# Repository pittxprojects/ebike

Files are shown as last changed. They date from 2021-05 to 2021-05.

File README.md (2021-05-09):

# DIY EBike Battery System

The main objective of this engineering project was to design a mount that allows a DIY E-bike to receive power from a commercial power tool battery. More specifically, we designed the mount to accept the RYOBI 40-Volt lithium-ion high-capacity battery. The intentions for this scope of design are as follows:

- Employ the economies of scale that are soon to come for lithium-ion batteries
- Take advantage of the safety features already incorporated in the battery
- Provide a battery solution for an E-bike that is easy to source and replace

Included in this repository is:
- A slide deck containing our written documentation on the project
- The Fusion 360 files of our part and the associated components
- The .stl files of our part for 3D printing

Our how-to video can be found [here].
## Authors & Contributors
_This project was conducted as part of the Spring 2021 XProject cohort. The XProjects are administered by the Innovation, Design, and Entrepreneurship Department at the Swanson School of Engineering at the University of Pittsburgh._

- Maya Roman – Junior ME Student
- Peter DeNicola – Junior ME Student
- John Rozzo – Sophomore EE Student
- Nick Bohn – Senior ME Student

- Stephen Spencer – Project Sponsor
- Brandon Barber – Project Coordinator
- Daniel Yates – Project Coordinator
- Dr. William Clark – Project Coordinator

- Thick Bikes (Pittsburgh, PA) – Bike Donor

## License



This work is licensed under a [Creative Commons Attribution-NonCommercial-ShareAlike 4.0 International License].

[//]: # (These are reference links used in the body of this note and get stripped out when the markdown processor does its job. There is no need to format nicely because it shouldn't be seen. Thanks SO - http://stackoverflow.com/questions/4823468/store-comments-in-markdown-syntax)

   [here]: <https://youtu.be/FgjxSFlo72g>
   [Creative Commons Attribution-NonCommercial-ShareAlike 4.0 International License]: <http://creativecommons.org/licenses/by-nc-sa/4.0/>

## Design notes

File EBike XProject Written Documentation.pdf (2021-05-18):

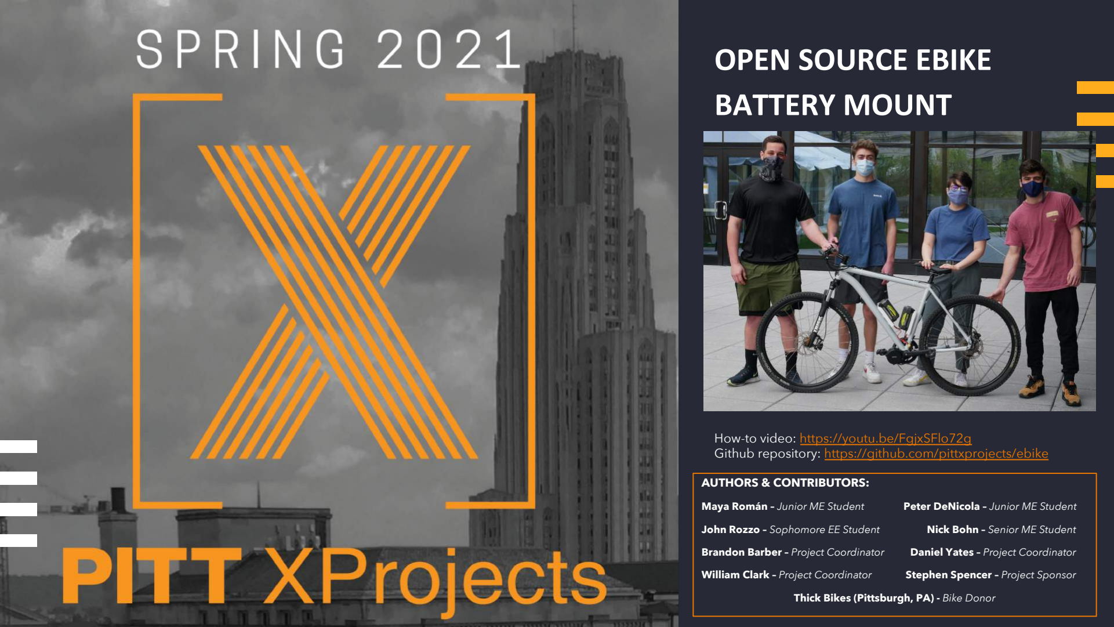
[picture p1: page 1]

### OPEN SOURCE EBIKE BATTERY MOUNT

AUTHORS & CONTRIBUTORS:
Maya Román – Junior ME Student | Peter DeNicola – Junior ME Student
John Rozzo – Sophomore EE Student | Nick Bohn – Senior ME Student
Brandon Barber – Project Coordinator | Daniel Yates – Project Coordinator
William Clark – Project Coordinator | Stephen Spencer – Project Sponsor
Thick Bikes (Pittsburgh, PA) - Bike Donor

How-to video: https://youtu.be/FgjxSFlo72g
Github repository: https://github.com/pittxprojects/ebike

### Project & General Design Overview

The main objective of this engineering project was to design a mount that allows a DIY E-bike to receive power from a commercial power tool battery. More specifically, we designed the mount to accept the RYOBI 40-Volt lithium-ion high-capacity battery. The intentions for this scope of design are as follows:

v Employ the economies of scale that are soon to come for lithium-ion batteries
v Take advantage of the safety features already incorporated in the battery v Provide a battery solution for an E-bike that is easy to source and replace

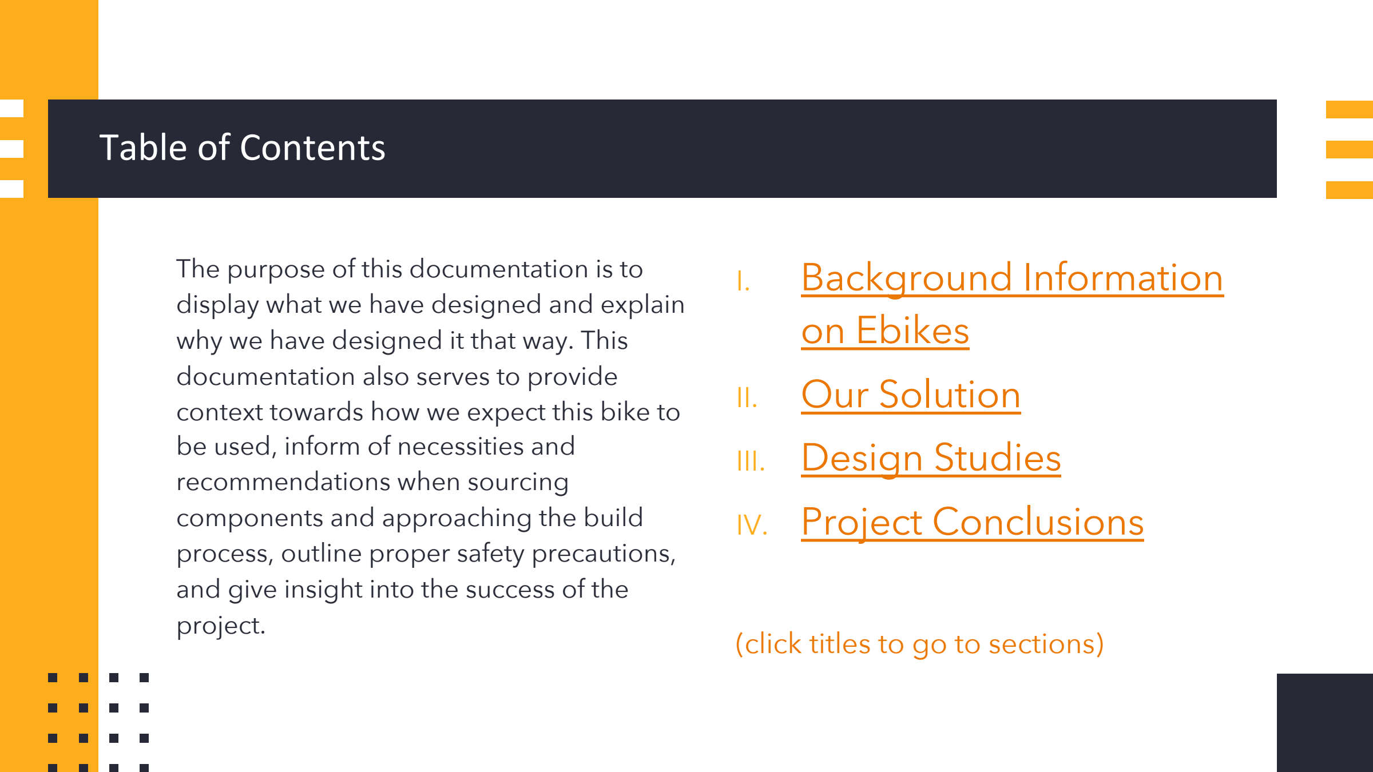
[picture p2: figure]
Table of Contents; The purpose of this documentation is to; why we have designed it that way. This documentation also serves to provide; be used, inform of necessities and recommendations when sourcing components and approaching the build; project.; I. Background Information on Ebikes II. Our Solution III. Design Studies IV. Project Conclusions; (click titles to go to sections)

display what we have designed and explain

context towards how we expect this bike to

process, outline proper safety precautions, and give insight into the success of the

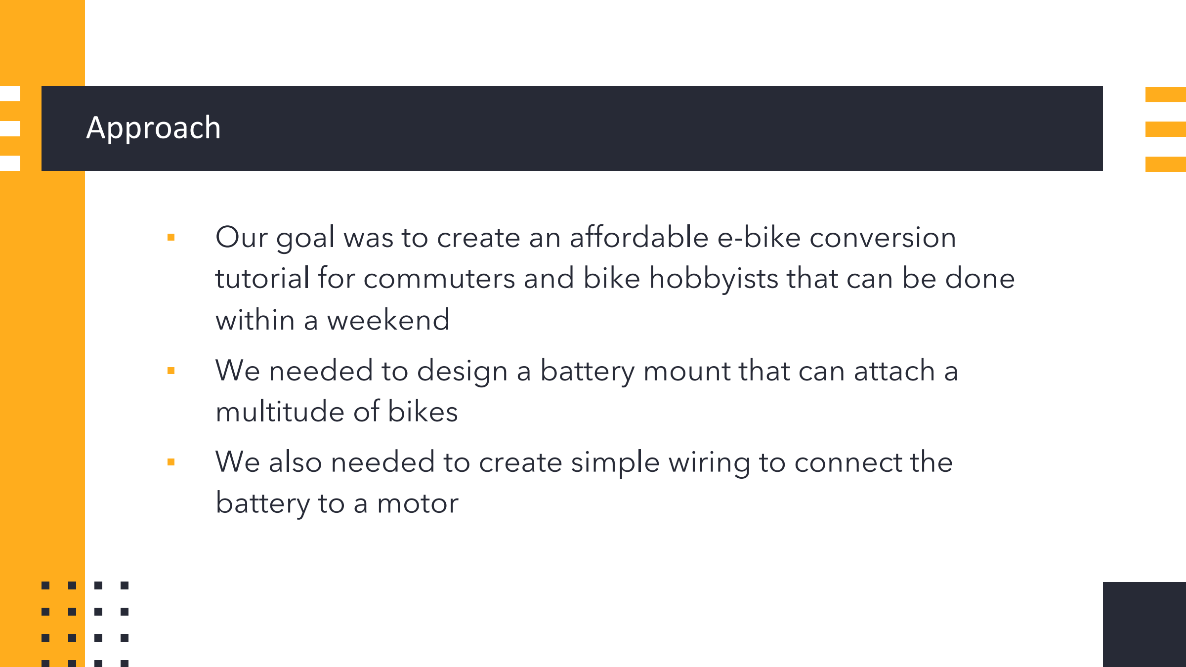
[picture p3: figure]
Approach; within a weekend; multitude of bikes; battery to a motor

### - Our goal was to create an affordable e-bike conversion tutorial for commuters and bike hobbyists that can be done

### - We needed to design a battery mount that can attach a

### - We also needed to create simple wiring to connect the

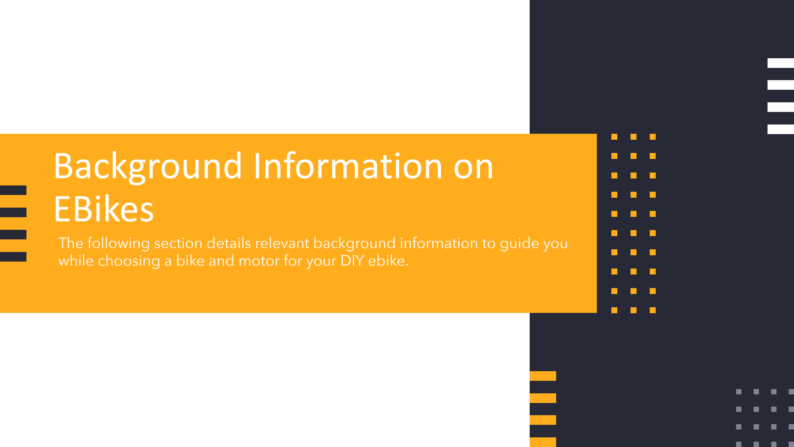
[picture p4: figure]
Background Information on EBikes

The following section details relevant background information to guide you while choosing a bike and motor for your DIY ebike.

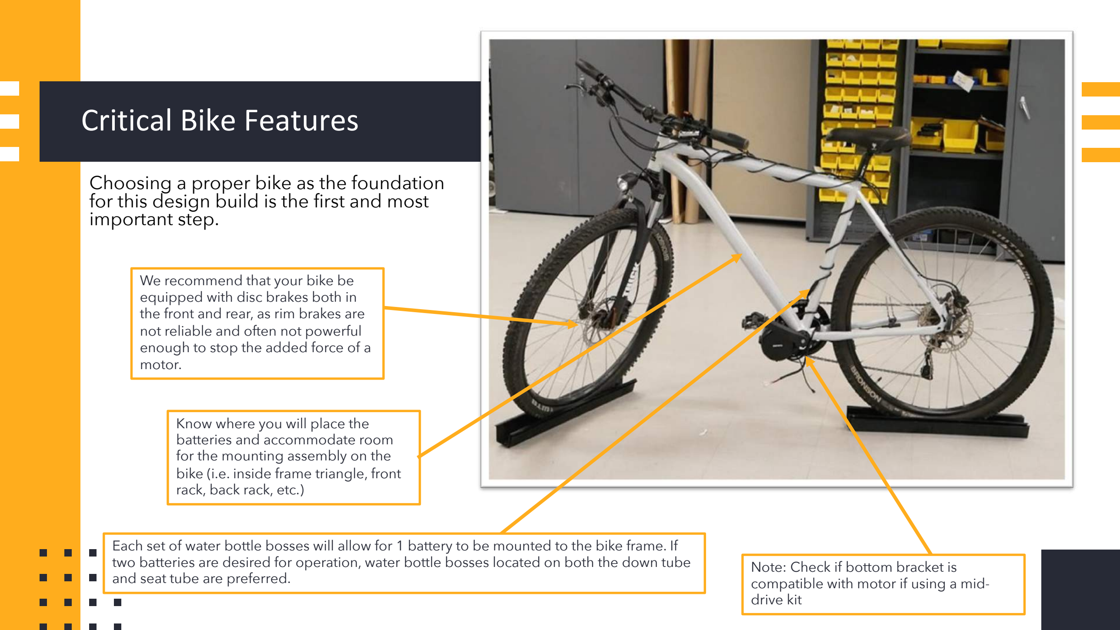
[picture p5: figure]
Critical Bike Features; important step.; We recommend that your bike be equipped with disc brakes both in the front and rear, as rim brakes are not reliable and often not powerful enough to stop the added force of a motor.; Know where you will place the batteries and accommodate room for the mounting assembly on the bike (i.e. inside frame triangle, front rack, back rack, etc.); and seat tube are preferred.; Note: Check if bottom bracket is compatible with motor if using a mid- drive kit

Choosing a proper bike as the foundation for this design build is the first and most

Each set of water bottle bosses will allow for 1 battery to be mounted to the bike frame. If two batteries are desired for operation, water bottle bosses located on both the down tube

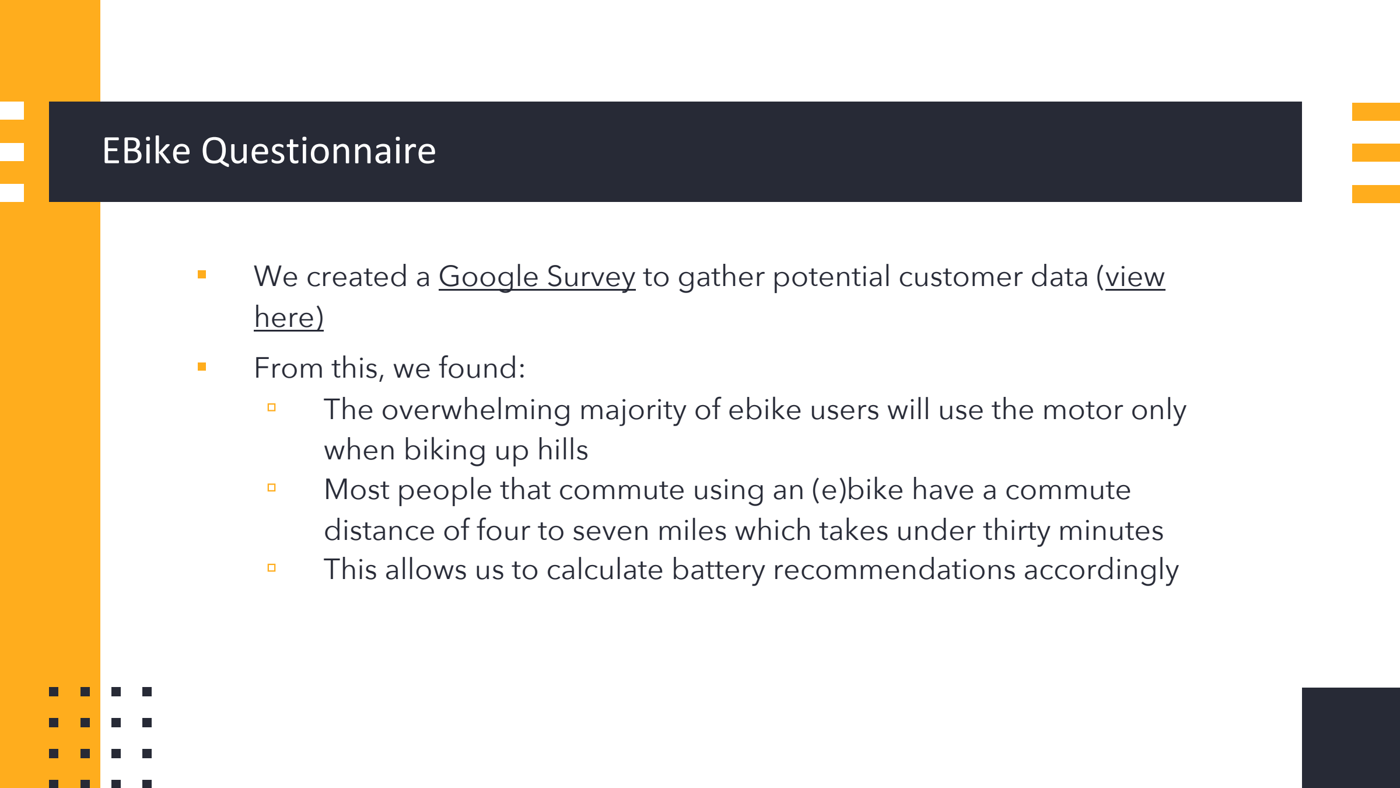
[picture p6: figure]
EBike Questionnaire; here) ▪ From this, we found:; when biking up hills

- We created a Google Survey (https://docs.google.com/forms/d/1E784Fk50arTw0hEiAAEJZYgr2MPm3P4Kt-JPYNBbJBc/edit) to gather potential customer data (view
- The overwhelming majority of ebike users will use the motor only
- Most people that commute using an (e)bike have a commute distance of four to seven miles which takes under thirty minutes
- This allows us to calculate battery recommendations accordingly

### Motor Selection

Motor Power Rating
If the use case of the motor is in a hilly area like Pittsburgh, a motor smaller than 500 W should not be considered. A 250 W motor would usually work for a rider less than 200 lbs if the use case is flat terrain. For very heavy riders, very steep and hilly terrain, or use cases where fast and very powerful performance is desired, 750-1000 W motors should be considered.

### Motor Selection

Peak Power
Additionally, one should consider the peak power (wattage) they will be able to receive with their combined motor and battery setup. This can be calculated by multiplying the Amperage rating of the motor controller (which determines the maximum current that can instantaneously be supplied to the motor) by the voltage of your battery setup. Usually, the peak power will be greater than the wattage that the motor is rated for. For example, a 500 W motor with a 25 Amp controller attached to a 40 V battery setup will experience a peak power of 1000 W. This will be an accurate representation of the power you can expect when you twist the throttle.
!"#$ %&'"( | = | *#+. *&-&( .&/-(&00"( #*% (#-1/2 | ∗ [5#--"(6 7&0-#2"]

### Motor Selection

Motor Type
There are two main types of motor styles used for powering ebikes:
Mid-drive
Mid-drive motors attach at the bike’s bottom bracket, driving the rear wheel in the same way the pedals drive the bike. Mid-drive motors allow you to shift through the bikes gears and provides high power.
Hub drive
Hub drive motors involve replacing one (or sometimes both) of your bike’s wheels with a wheel with a motor at the hub.

### Motor Selection

Mid-Drive Motor | Hub Motor
Higher torque/power since motor directly drives the crank | Decreased torque/performance due to more losses since motor drives rear or front wheel
Maintenance and service is very easy | Service can be complicated for even changing a flat tire
Improved handling by positioning close to the bikes center of gravity creating the feel of riding a traditional bike | Weight is distributed unevenly across the bike either towards the front or rear tire, creating an unnatural ride
Expensive | Cost-effective

### Battery Selection

The problem presented to us by our sponsor related to battery selection for DIY ebikes. People converting bikes to ebikes on their own face the decision to spend a lot of money on proprietary batteries that are large and expensive, or spend less money on less safe batteries. The power tool battery chosen for this project was a RYOBI 40V 4Ah due to the brands popularity and reputation, and battery availability.

### Battery Selection

Battery Overview | Price per Kilowatt hour Comparison (based on large home improvement retailer pricing)
| RYOBI 40V 7.5Ah | $763.33/kWh
| RYOBI 40V 6Ah | $745.82/kWh
| RYOBI 40V 5Ah | $795.00/kWh
| RYOBI 40V 4Ah | $900.00/kWh
| RYOBI 40V 2Ah | $1237.50/kWh

Our sponsor had us
use two RYOBI 40V
4Ah batteries to power
the bike.
(Battery Manual) (https://images.thdstatic.com/catalog/pdfImages/35/357388b5-188b-4d52-b208-4c9af14d54f3.pdf)

### Range Calculations

You can estimate your range based on your battery combination’s total energy capacity and your ebike’s efficiency based on your riding conditions.
Energy Capacity:
The power your battery selection can provide your ebike is based on the batteries’ voltage, their Ah capacity, and how many batteries you use.
!"#$% | = | '"()*+$ | ∗ | -*!*-.)/ | ∗ | # "1 2*))$%.$3
In our case, with two 40V, 4Ah batteries, our battery system would be capable of providing 320 Wh of energy in one charge:
40 6 ∗ 4 7ℎ ∗ (2 2*))$%.$3) = 320 =ℎ

Efficiency:
On average, going 20mph on flat terrain, an ebike has an efficiency of about 25Wh/mi using just the throttle, with no pedal contribution. The efficiency while using pedal assist, but still assuming a speed of 20mph on flat terrain is closer to 15Wh/mi.
Many factors affect the actual efficiency, including total load (weight of rider, bike, and cargo), wind speed and direction, road conditions (paved, gravel, dirt, etc), aerodynamics of your bike, hill grades, etc.
Check out this page (https://www.ebikeaholic.org/ebike-range-calculator) for a more in depth efficiency estimation.

### Range Calculations

Total Range:
To find your battery combination’s total range on one charge, simply divide the energy capacity by the efficiency.

!"#$%&#!' (&)*! =

[!)!(*- .&/&.$#-]
[!"#$%&#!' !11$.$!).-]

This means that in our case, with two 4Ah 40V batteries, we would have a range of about 12.8 miles using just the throttle, and about 21.3 miles if we use pedal assist – assuming we’re going 20mph on flat terrain.
320 5ℎ
25 5ℎ/%$

= 12.8 %$<!" #ℎ(=##<! =)<-

320 5ℎ
15 5ℎ/%$

= 21.3 %$<!" >$#ℎ /!'&< &""$"#

Use these calculations as guidelines rather than hard rules to help you decide which battery or battery combination to use. Remember to give yourself a margin between the range you need and the range your battery system can provide.

# Our Solution

The following section details the specifics of how to make our DIY Battery System. This section supplements our how-to video. (https://youtu.be/FgjxSFlo72g)

### Our Battery System

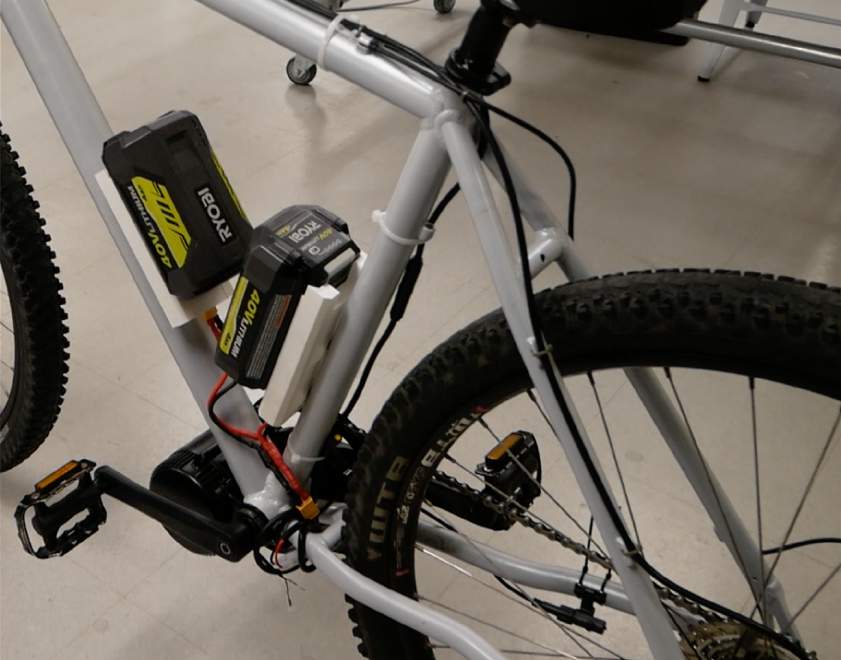
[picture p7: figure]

Our system consists of two RYOBI 40V 4Ah lithium ion batteries attached to the ebike via mounts we designed that connects in parallel to the motor via a Y-harness.

### Our Battery System

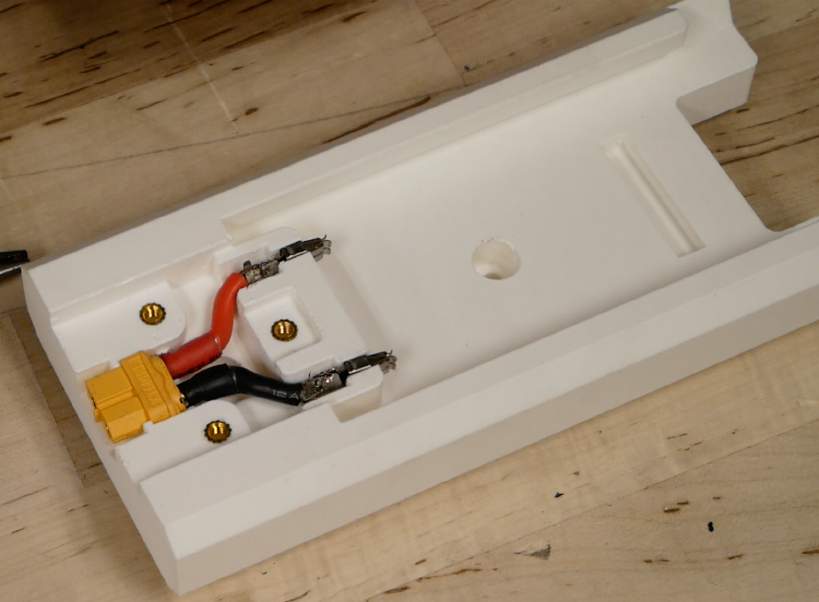
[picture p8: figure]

The mount features rails for the battery to slide into, a slot for the battery’s latch to lock into, two mounting holes to attach the mount to the bike, geometry to hold the internal harness in place and mounting points for a wire cover.

### Critical Dimensions

The critical dimensions of the battery mount are ones we caution against changing if you adjust the CAD model or design your own based on ours. These dimensions are detailed in the next slide, and the critical dimension drawing on our Github repository. The key dimensions are the battery mating profile, the size and position of notches for power timer tabs, the position of power timer timer slots in relation to each other and the locking tab, and the height between the top face that touches the battery and the mounting point on bike (for hand access to battery release tab)

### Critical Dimensions

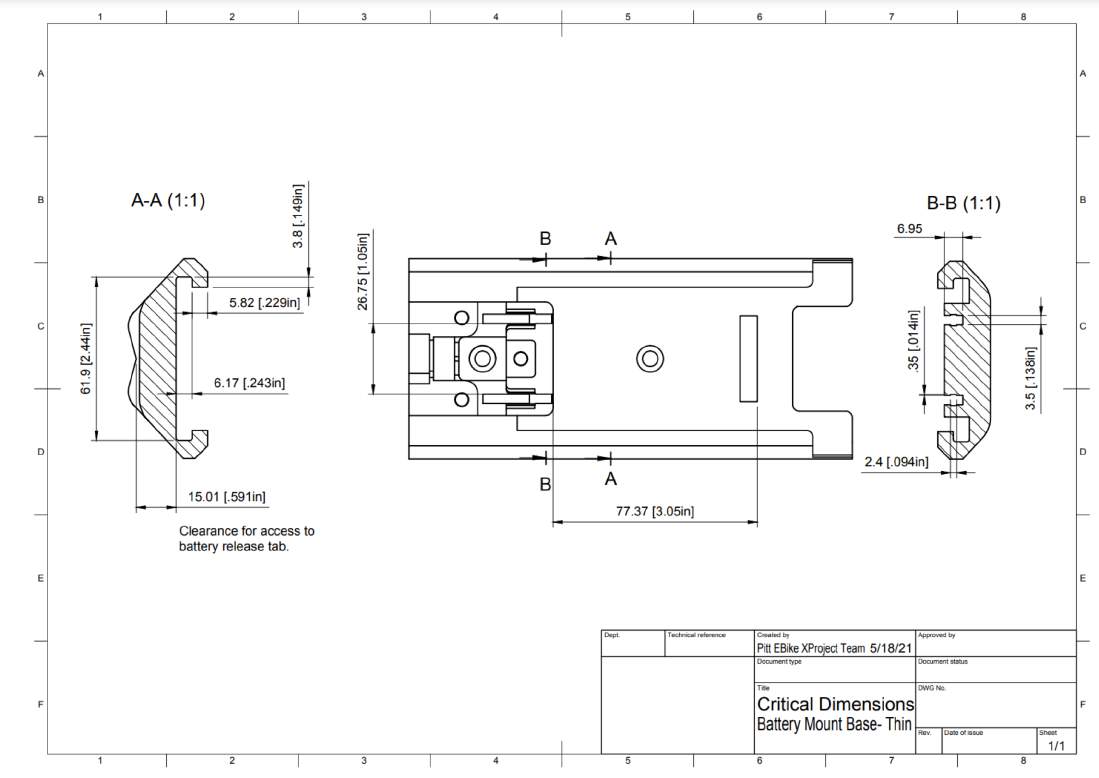
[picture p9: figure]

Bill of Materials

Item | Qty | Vendor | Link | Unit Price | Total Price
M5x0.8 12mm bolts | 4 | McMaster-Carr | https://www.mcmaster.com/92095A210/ | $8.66/50 | $8.66
6-32 ½" bolts | 6 | McMaster-Carr | https://www.mcmaster.com/91251A148/ | $9.59/100 | $9.59
Heat set threaded inserts for 6-32 bolts | 6 | McMaster-Carr | https://www.mcmaster.com/94459A280/ | $10.12/50 | $10.12
24-12 AWG stranded wire (more on wire sizing later) | ~1ft black, ~1ft red | Amazon | https://www.amazon.com/BNTECHGO-Silicone-Flexible-Strands-Stranded/dp/B01ABOPMEI (https://www.amazon.com/BNTECHGO-Silicone-Flexible-Strands-Stranded/dp/B01ABOPMEI) | $12.98/20ft | $12.98
XT60 connector pair, male and female | 3 pairs | Amazon | https://www.amazon.com/Upgrade-Female-Bullet-Connectors-Battery/dp/B07VRZR5TL (https://www.amazon.com/Upgrade-Female-Bullet-Connectors-Battery/dp/B07VRZR5TL) | $8.99/12 pairs | $8.99
Standard power timer contacts | 4 | Digi-Key | (10-11 AWG) (https://www.digikey.com/en/products/detail/te-connectivity-amp-connectors/963709-1/2332255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) (11-13 AWG) (https://www.digikey.com/en/products/detail/te-connectivity-amp-connectors/927824-2/2332032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) (13-17AWG) (https://www.digikey.com/en/products/detail/te-connectivity-amp-connectors/927833-1/2332041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) | $00.74 $00.40 $00.30 | $2.96
3D printer filament (Village Plastics PLA) | ~59m | - | - | - | -
Heat shrink (we used 3/8" and ¼" 3:1) | ~16 pieces | Amazon | https://www.amazon.com/Wirefy-275-Heat-Shrink-Tubing/dp/B084GWYX42 (https://www.amazon.com/Wirefy-275-Heat-Shrink-Tubing/dp/B084GWYX42) | $13.95/275 pcs | $13.95
Solder | - | - | - | - | -
RYOBI 40V 4Ah batteries | 2 | Home Depot | https://www.homedepot.com/p/RYOBI-40-Volt-Lithium-Ion-4-Ah-High-Capacity-Battery-OP4040A1/307973316 (https://www.homedepot.com/p/RYOBI-40-Volt-Lithium-Ion-4-Ah-High-Capacity-Battery-OP4040A1/307973316) | $144 | $288
BAFANG 500W mid-drive motor kit | 1 | Amazon | https://www.amazon.com/gp/product/B07PQM7167/ref=ppx_yo_dt_b_asin_title_o04_s00?ie=UTF8&psc=1 (https://www.amazon.com/gp/product/B07PQM7167/ref=ppx_yo_dt_b_asin_title_o04_s00?ie=UTF8&psc=1) | $404 | $404
Donor bike | 1 | - | - | - | -
TOTAL | $759.25

### Bill of Materials

- Note on the BOM: the only item we recommend being exactly the same as what we used are the power timer contacts which interface with the battery terminals. All other materials can be what you have on hand or find at a hobby store or website. We provided the material links more as a helpful reference than as the exact places you must buy parts.

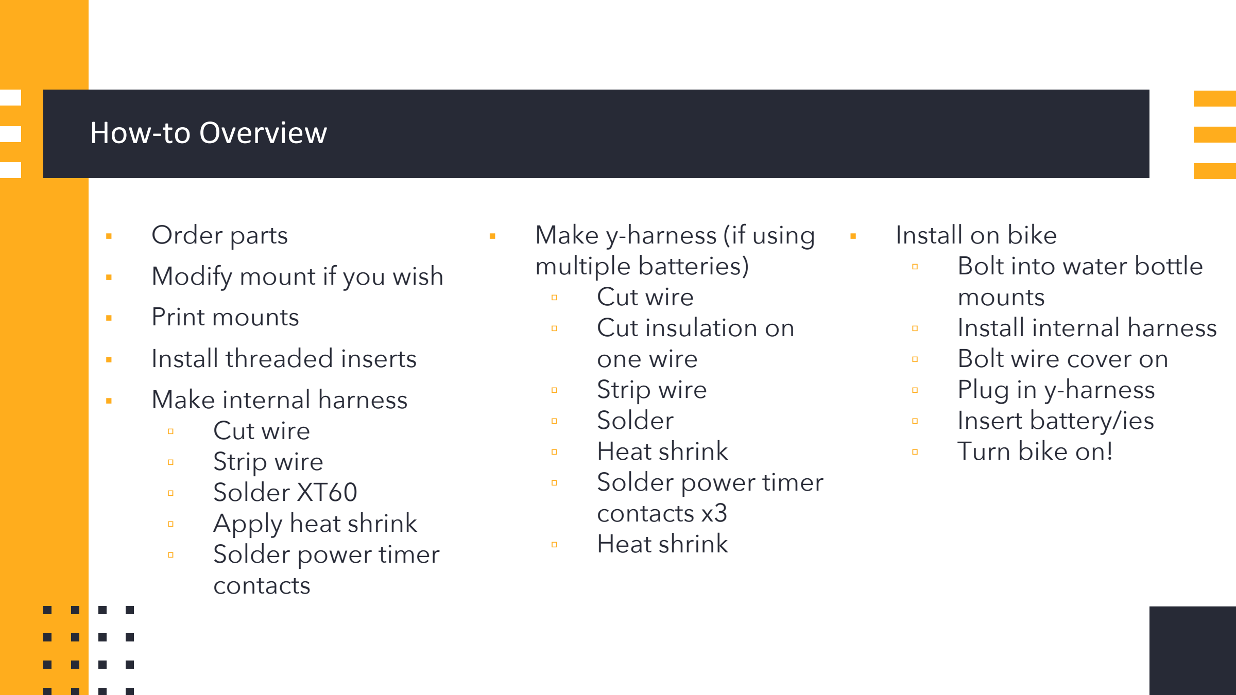
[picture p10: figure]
How-to Overview; ▪ Order parts ▪ Modify mount if you wish ▪ Print mounts ▪ Install threaded inserts ▪ Make internal harness ▫ Cut wire ▫ Strip wire ▫ Solder XT60 ▫ Apply heat shrink ▫ Solder power timer contacts; ▪ Make y-harness (if using multiple batteries) ▫ Cut wire ▫ Cut insulation on one wire ▫ Strip wire ▫ Solder ▫ Heat shrink ▫ Solder power timer contacts x3 ▫ Heat shrink; ▪ Install on bike ▫ Bolt into water bottle mounts ▫ Install internal harness ▫ Bolt wire cover on ▫ Plug in y-harness ▫ Insert battery/ies ▫ Turn bike on!

### Order Parts

- You can use our Bill of Materials as a reference for your project, however you don’t have to use all of the same exact parts as we did.
- It’s probably a good idea to get a few extra of the components like the threaded inserts, the power timer contacts, and the XT60 connectors if possible just in case something goes wrong while putting it all together
- Make sure the get heat shrink and power timer contacts that are compatible with your chosen wire gauge
- The next slide details how to choose your wire gauge

### Electrical Safety

Loose connections, power overloads (excessive current), and short circuiting can all melt your wire and cause electrical safety hazards!
To prevent excessive current draw, you must use wires properly rated for current that you expect to put through them.
Ideally, your battery system should be the current-limiting factor in your ebike system, meaning the total amerage capacity of your battery(ies) should be greater than the max current your motor controller is rated for.
That was not the case for our setup, and our motor controller was rated for a maximum of 25 Amps, so we used 12 AWG wire to incorporate a margin of safety in the worst case scenario of maximum current draw.
Use the chart on the right (from here) (https://www.engineeringtoolbox.com/wire-gauges-d_419.html) to help you determine which wire gauge is appropriate for the current that will go through your system.

Max. Current
Load (amps)

### Modify the Model

- The default model allows you to mount two 40V 4Ah RYOBI batteries on both sets of water bottle mounting points, however you can edit the model to function as you need. You can download the Fusion 360 models from our Github repository. (https://github.com/pittxprojects/ebike)
- To move the mounting hole position in the model, edit Sketch 11
- To remove the v-notch geometry, suppress Extrude 13
- You'll have to edit the counterbore in Hole 1 so that there’s enough thickness for the two mounting bolts to clamp on to
- To adjust the battery mating geometry, edit Sketch 2, renamed “battery mating geometry”

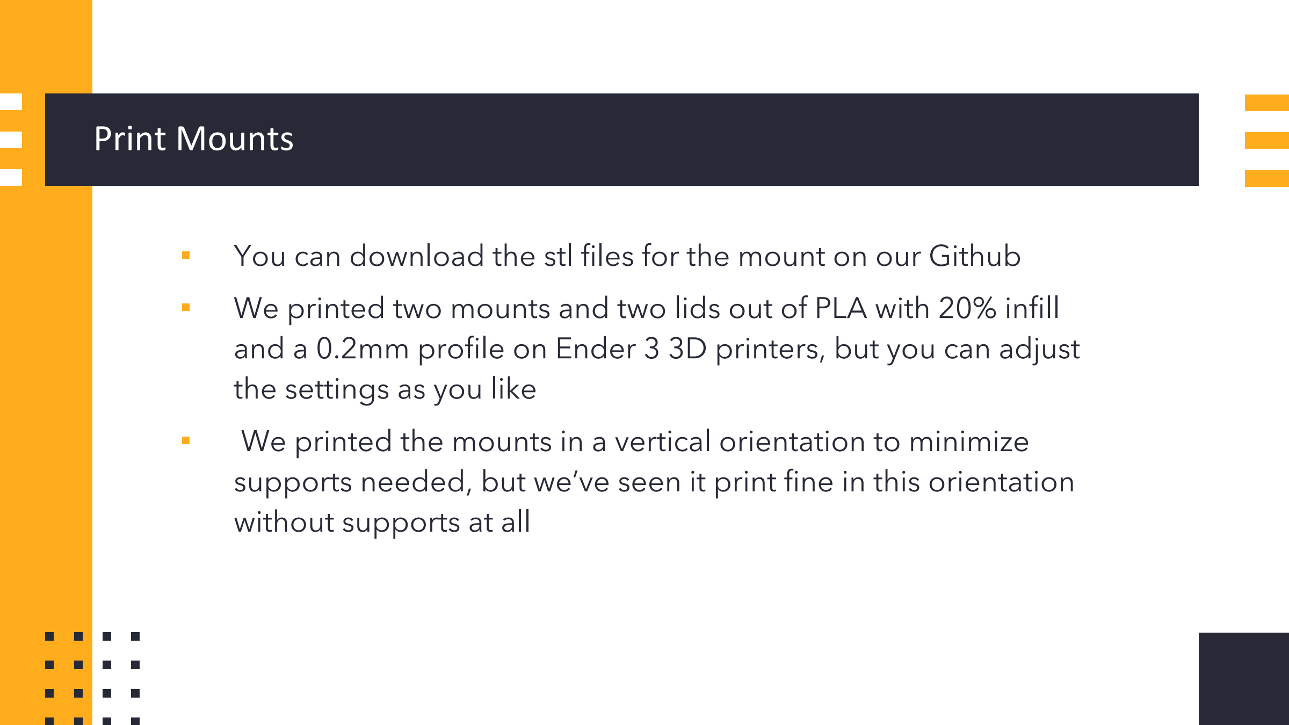
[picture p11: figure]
Print Mounts; the settings as you like; without supports at all

- You can download the stl files for the mount on our Github
- We printed two mounts and two lids out of PLA with 20% infill and a 0.2mm profile on Ender 3 3D printers, but you can adjust
- We printed the mounts in a vertical orientation to minimize supports needed, but we’ve seen it print fine in this orientation

### Install Threaded Inserts

- To bolt the lid to the mount, you’ll need to install threaded inserts into the mount
- You can use a soldering iron (since the holes for the inserts go all the way through the part you can use a regular soldering iron tip) to heat the insert while it’s sitting in the hole, gently pressing down until the insert is 90% of the way down
- Then remove the soldering iron, and use something flat and heat resistant to press down on the threaded insert, so it’s flush with the top face
- Press down for about 10 seconds, by which the plastic surrounding the insert should have cooled enough
- Repeat for the other two holes
- Watch us perform the technique in our video, or read more about it here (https://hackaday.com/2019/02/28/threading-3d-printed-parts-how-to-use-heat-set-inserts/)

### Make Internal Harness

- To make the internal harness you’ll need two pieces of wire, one 1 ¼ in length, and one 1 5/8 in length. It doesn’t matter which is which, but it will make installation into the mount easier.
- Strip about a quarter of an inch of insulation off both ends of both wires.
- Solder the wires to a female XT60 connector. Make sure the wires are soldered onto the correct side of the connector, each side should be labeled as + or -.
- Use up to ½ in of heat shrink on each wire where its soldered to the connector. The heat shrink mitigates possible shorting, but use too much and the small wires will be difficult to bend.
- Solder the power timer contacts to the other ends of the wires. While soldering, make sure not to clamp onto the tabs that come out of the wider sides of the contact, otherwise they won’t snap into place in the mount properly.

### Make Internal Harness

- You can crimp the contacts if you have the right kind of crimping tool. Otherwise it helps to use pliers to pinch the contact around the wire before you solder.
- Additionally, before you solder, make sure to orient the contact as shown below so that it’s easy to install into the mount. Notice the orientation of the power timer contact slot in relation to the XT60
- We don’t recommend adding heat shrink to
wire’s connection to the power timer contact
because when installed the contacts can’t short to each other, and the heat shrink makes it too stiff to install easily.

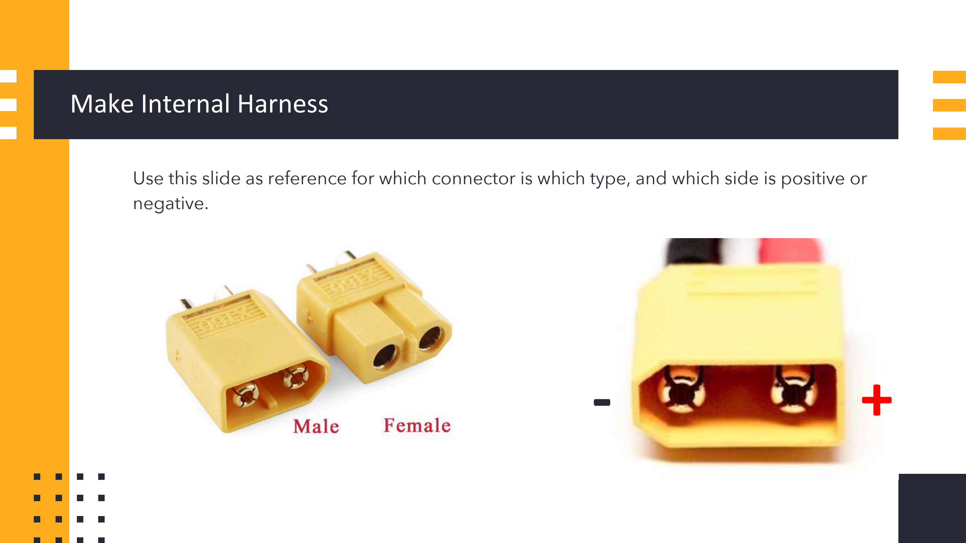
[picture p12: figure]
Make Internal Harness; negative.

Use this slide as reference for which connector is which type, and which side is positive or

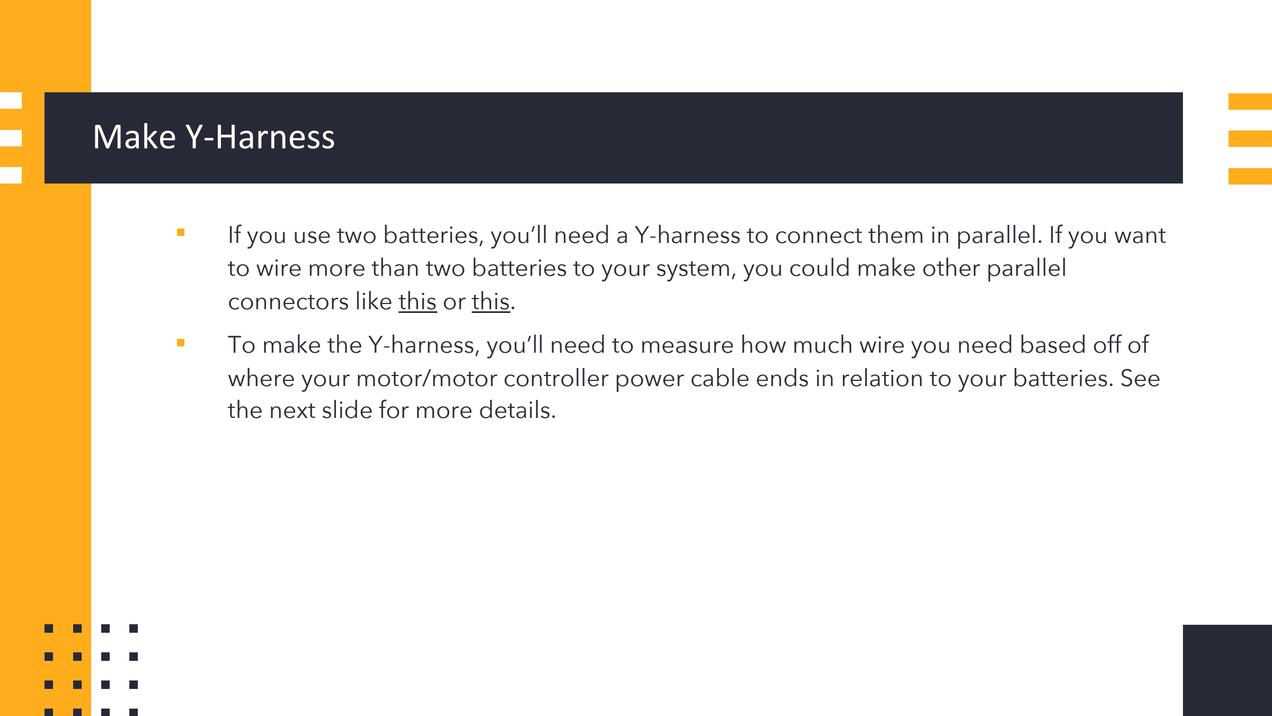
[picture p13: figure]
Make Y-Harness; connectors like this or this.; the next slide for more details.

- If you use two batteries, you’ll need a Y-harness to connect them in parallel. If you want to wire more than two batteries to your system, you could make other parallel
- To make the Y-harness, you’ll need to measure how much wire you need based off of where your motor/motor controller power cable ends in relation to your batteries. See

### Make Y-Harness

- You’ll need two sets of wires for the Y-harness, each set needs one ground and one positive wire of the same length.
- Approximate how long the blue wire would need to be on your bike – from the connector to one battery - add some length for slack, and cut one set to that length
- Then approximate how long the pink wire would need to be – from any point on the first wire to the second battery. Add some length to that value for slack, and cut the second set to length

### Make Y-Harness

- Now, using a knife, cut out a section of the insulation on the longer wires at the location where you want the second wire to connect (where the pink and blue wire intersect in the previous diagram). The cut out only needs to be 1-2 inches wide.
- Strip the wire at both ends of all wires.
- Solder one end of the shorter wire to the exposed section of the longer wire. We found this method to be easier than soldering the ends of three wires together given the larger wire gauge size we used. Repeat with the second set of wires.
- Use heat shrink to cover the solder joints.
- Solder the end of the wires going to the motor to a female XT60 connector, and solder the two ends going to the batteries to male XT60 connectors. See the next slide for reference. Make sure the polarity of the XT60 connectors is correct.
- Use heat shrink to cover the solder joints on all of the XT60 connectors.

### Make Y-Harness

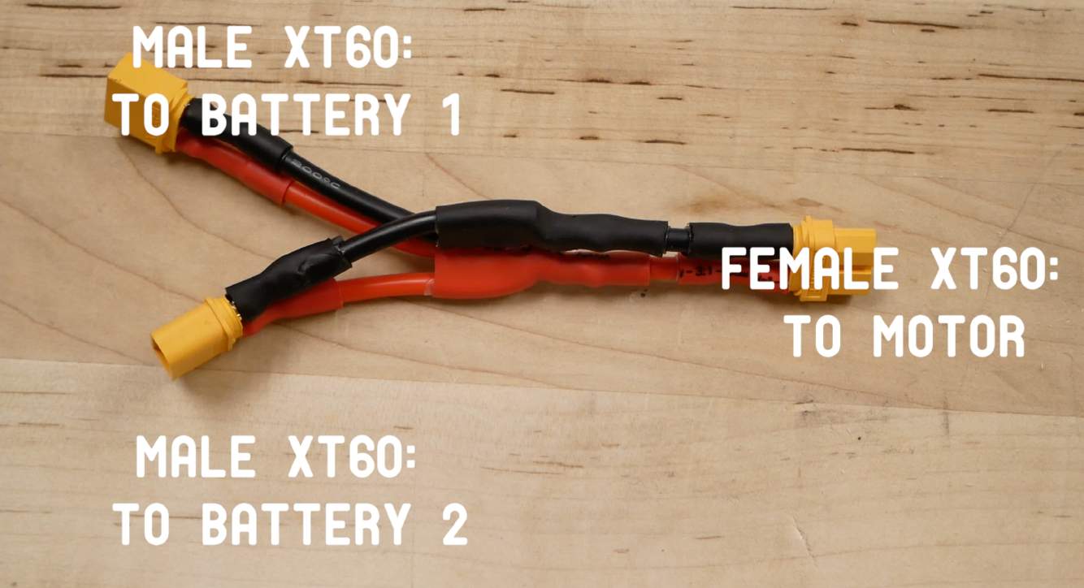
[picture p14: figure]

### Install on Bike

- First, bolt the 3D printed mounts onto the water bottle mounts using the M5 bolts. Make sure the opening to slide the battery in is at the top of the mount.
- Next, install the internal harness into each mount. The contact going to the ground wire should go in the right and the contact on the positive wire should go in the left.
- Start with whichever wire is longer, and slide the contact into its groove until you hear a click. The tabs on either side of the contact should have snapped into place in the mount. Repeat with the other contact.
- Snap the XT60 connector into its slot, then install the wire cover by bolting it down with the three 6-32 bolts into the threaded inserts.
- After installing both internal harnesses and wire covers, use the Y-harness to connect the mounts in parallel to the motor.
- Insert the batteries, turn the bike on, and enjoy your new ebike!

# Design Studies

We identified the four most critical aspects of the design, and conducted design studies to investigate each aspect

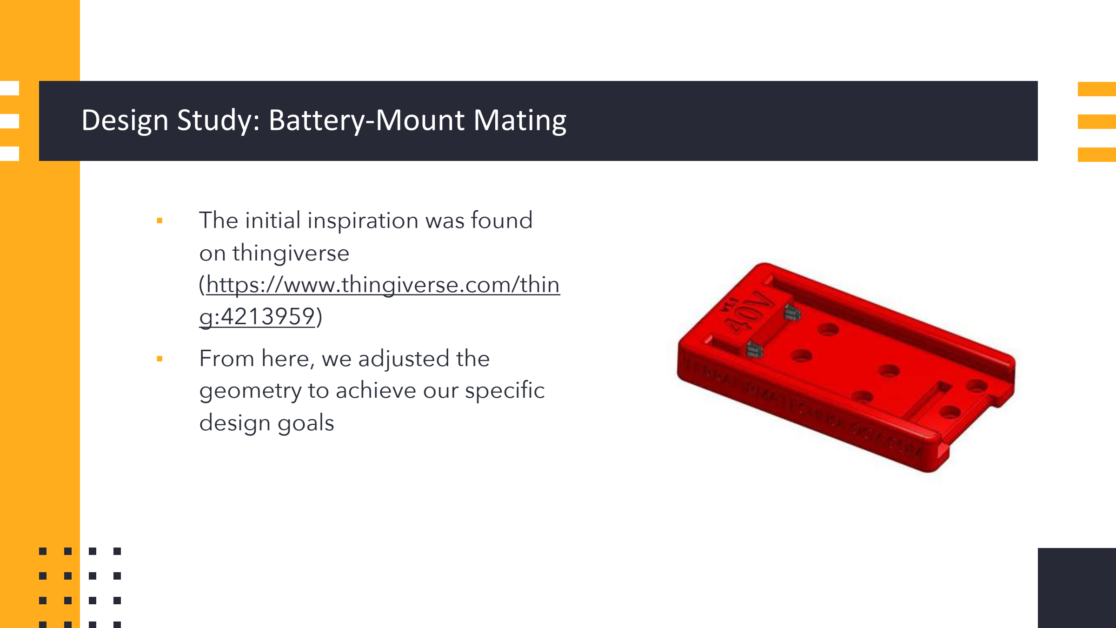
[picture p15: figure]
Design Study: Battery-Mount Mating; ▪ The initial inspiration was found on thingiverse (https://www.thingiverse.com/thin g:4213959) ▪ From here, we adjusted the geometry to achieve our specific design goals

### Design Study: Battery-Mount Mating

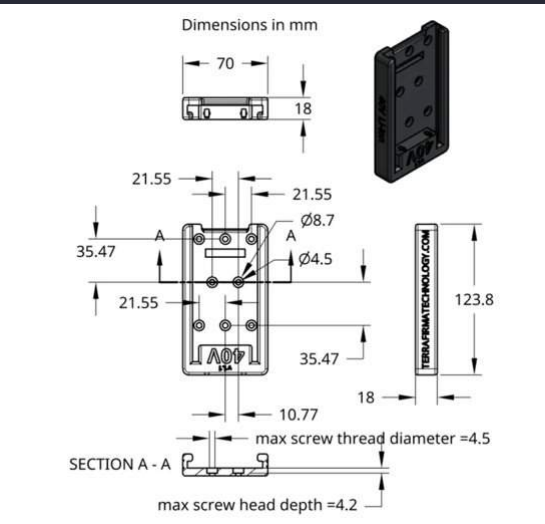
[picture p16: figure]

- Dimensions we adopted and modified for our design

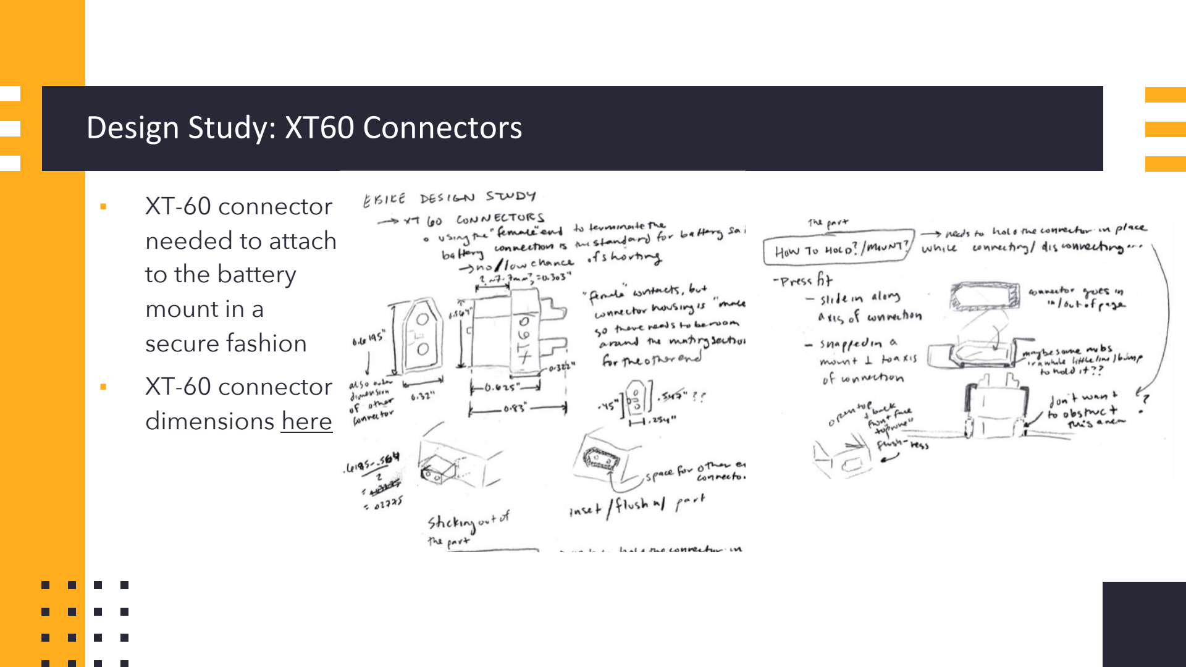
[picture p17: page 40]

### Design Study: XT60 Connectors

- XT-60 connector
needed to attach
to the battery
mount in a
secure fashion
- XT-60 connector
dimensions here (https://cdn.sparkfun.com/datasheets/Prototyping/xt60.pdf)

1st iteration | 2nd iteration

3rd (final) iteration
- Includes notches to
hold in XT connector
well
- Two parts to design
- Main block that
represents the battery
mount
- Screw on lid with
notches

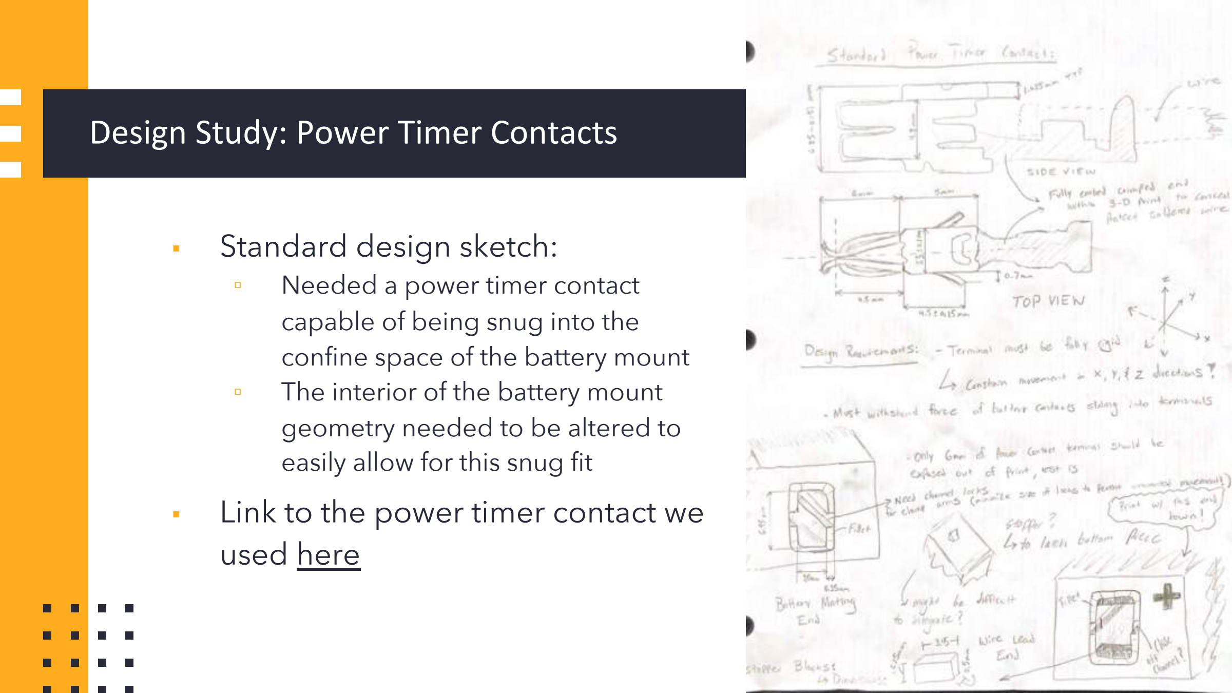
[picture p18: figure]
Design Study: Power Timer Contacts; ▪ Standard design sketch: ▫ Needed a power timer contact capable of being snug into the confine space of the battery mount ▫ The interior of the battery mount geometry needed to be altered to easily allow for this snug fit ▪ Link to the power timer contact we used here
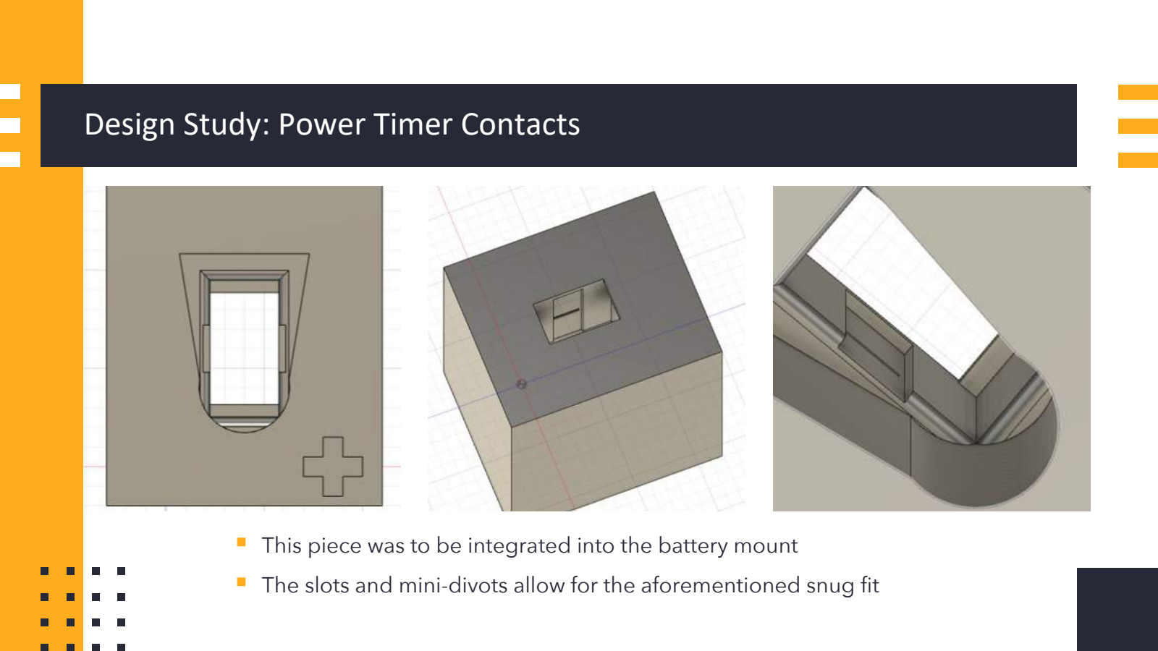
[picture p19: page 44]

### Design Study: Power Timer Contacts

- This piece was to be integrated into the battery mount
- The slots and mini-divots allow for the aforementioned snug fit

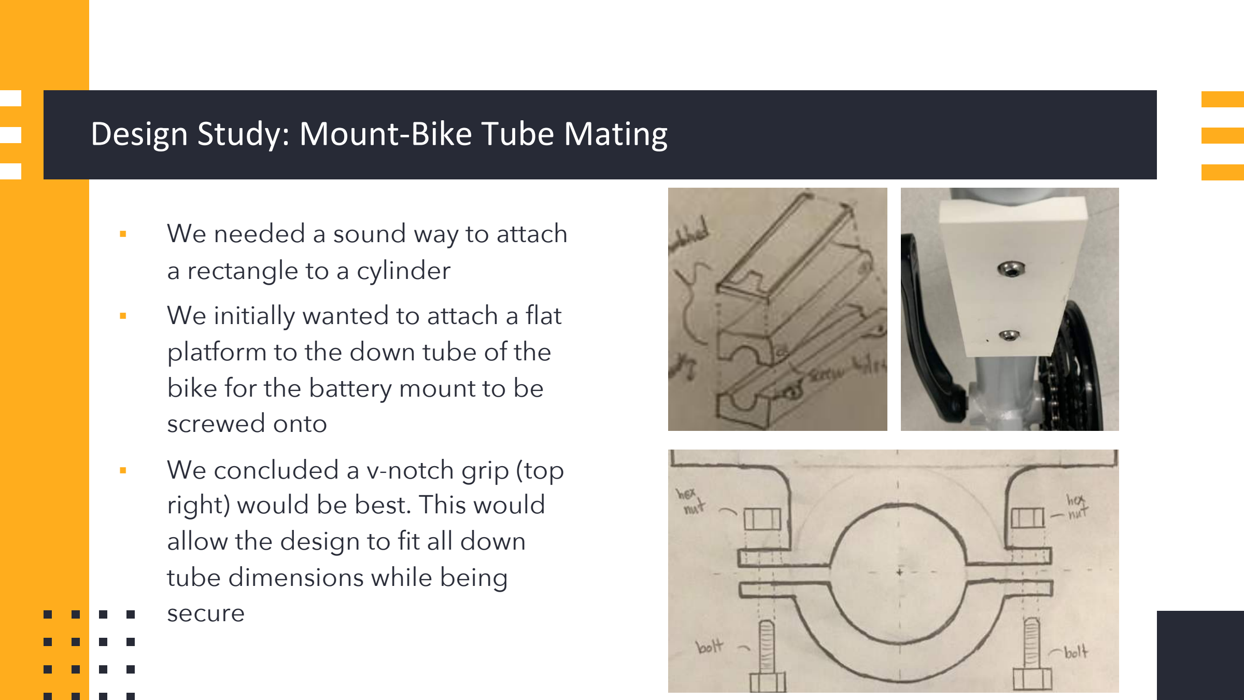
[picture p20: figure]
Design Study: Mount-Bike Tube Mating; ▪ We needed a sound way to attach a rectangle to a cylinder ▪ We initially wanted to attach a flat platform to the down tube of the bike for the battery mount to be screwed onto ▪ We concluded a v-notch grip (top right) would be best. This would allow the design to fit all down tube dimensions while being secure

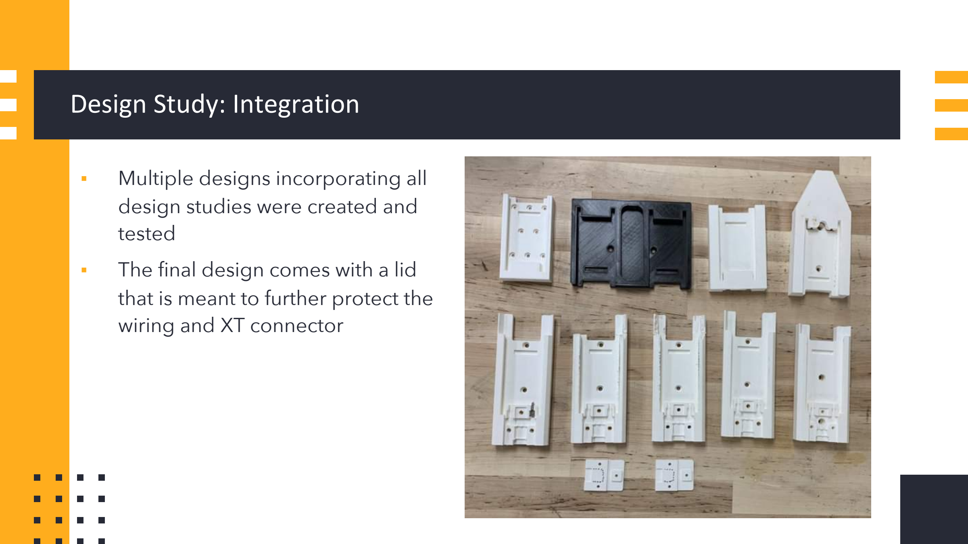
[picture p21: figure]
Design Study: Integration; ▪ Multiple designs incorporating all design studies were created and tested ▪ The final design comes with a lid that is meant to further protect the wiring and XT connector

# Project Conclusions

Final thoughts and points to wrap up the project.

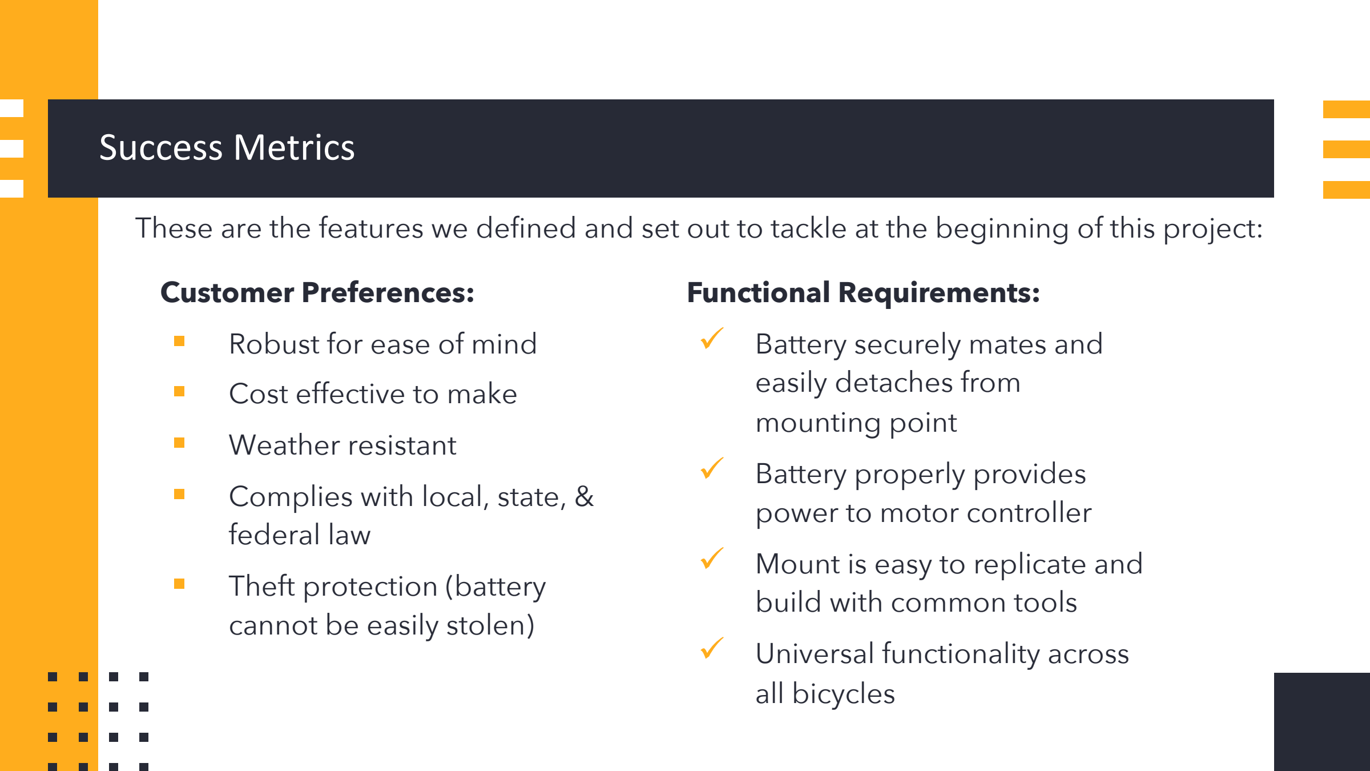
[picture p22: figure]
Success Metrics; Customer Preferences: • Robust for ease of mind • Cost effective to make • Weather resistant • Complies with local, state, & federal law • Theft protection (battery cannot be easily stolen); Functional Requirements: ü Battery securely mates and easily detaches from mounting point ü Battery properly provides power to motor controller ü Mount is easy to replicate and build with common tools ü Universal functionality across all bicycles

These are the features we defined and set out to tackle at the beginning of this project:

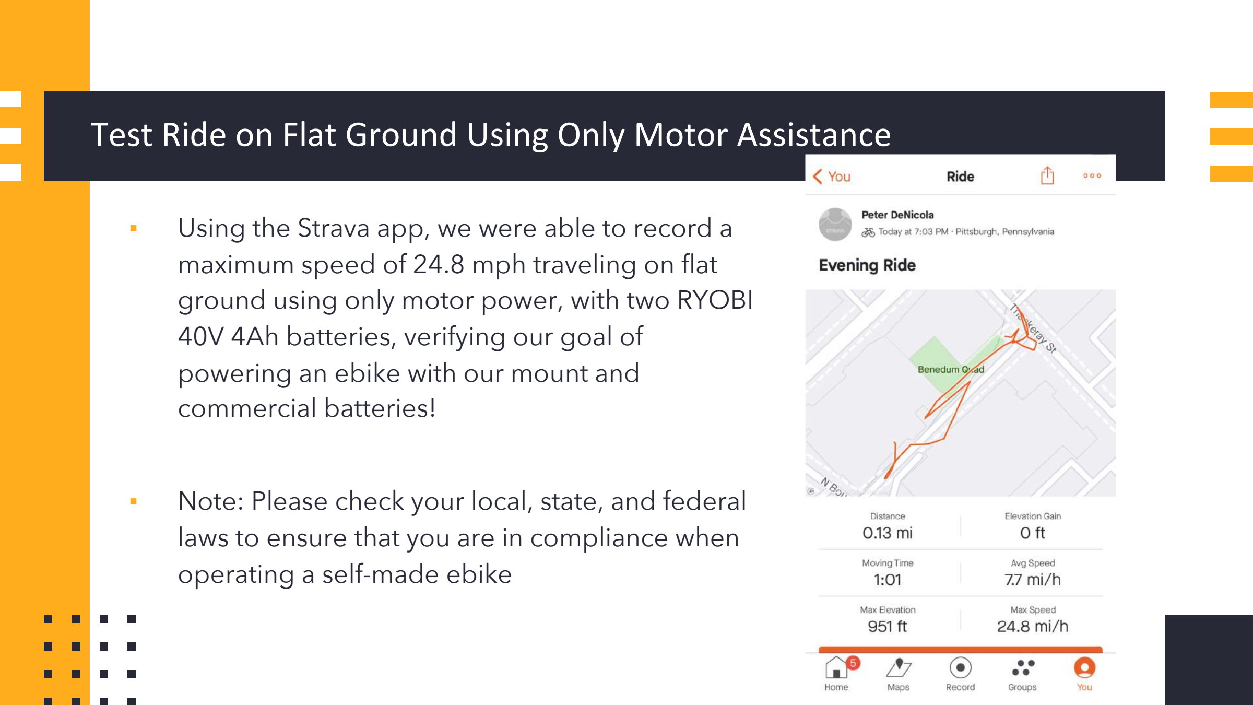
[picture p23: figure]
powering an ebike with our mount and commercial batteries!; operating a self-made ebike

### Test Ride on Flat Ground Using Only Motor Assistance

- Using the Strava app, we were able to record a
maximum speed of 24.8 mph traveling on flat ground using only motor power, with two RYOBI 40V 4Ah batteries, verifying our goal of
- Note: Please check your local, state, and federal laws to ensure that you are in compliance when

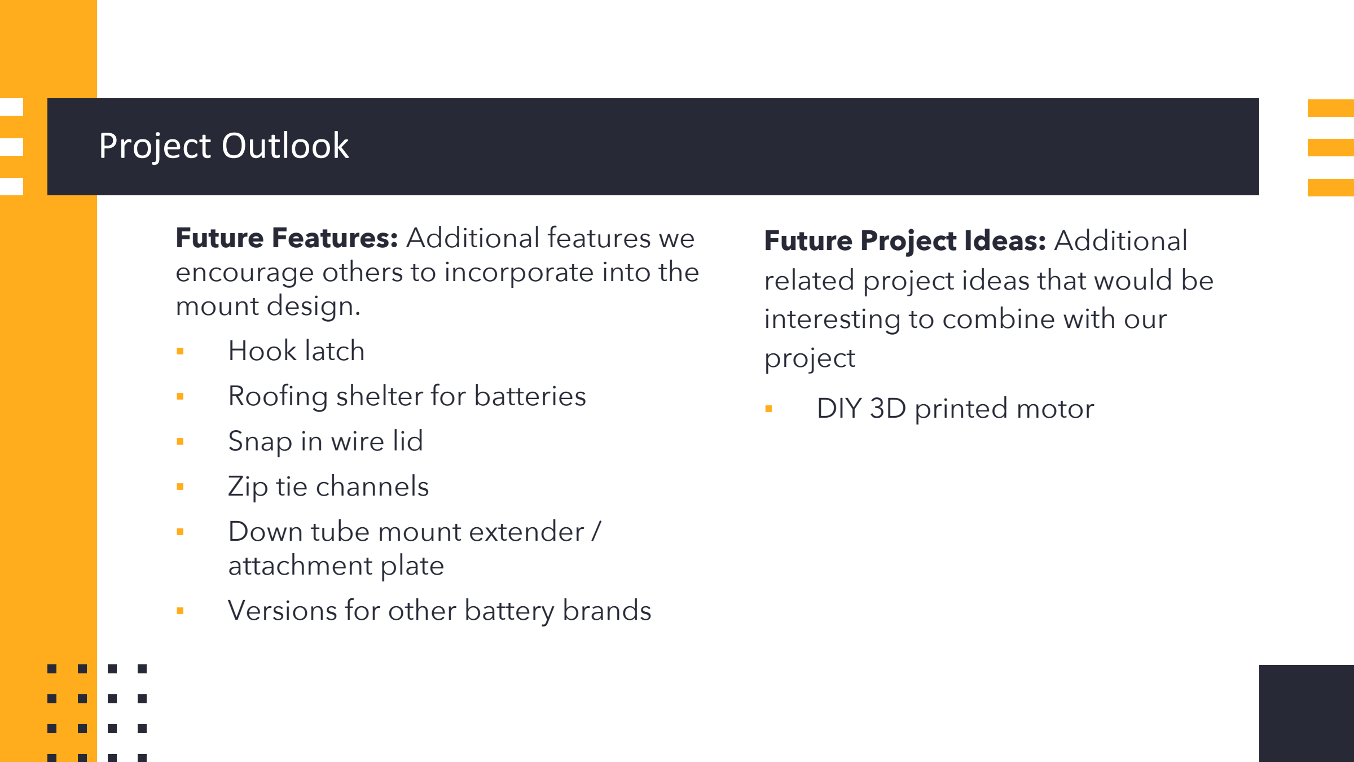
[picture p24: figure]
Project Outlook; Future Features: Additional features we; mount design. ▪ Hook latch ▪ Roofing shelter for batteries ▪ Snap in wire lid ▪ Zip tie channels ▪ Down tube mount extender / attachment plate ▪ Versions for other battery brands; Future Project Ideas: Additional related project ideas that would be interesting to combine with our project ▪ DIY 3D printed motor

encourage others to incorporate into the

## Thank You to All Involved!

## Project sponsor and mentor: Stephen Spencer

## Bike donation: Thick Bikes (Pittsburgh

PA)

Project coordinators: William Clark,

## Brandon Barber, & Daniel Yates

Student contributors: Maya Román,

## Peter DeNicola, John Rozzo, Nick Bohn

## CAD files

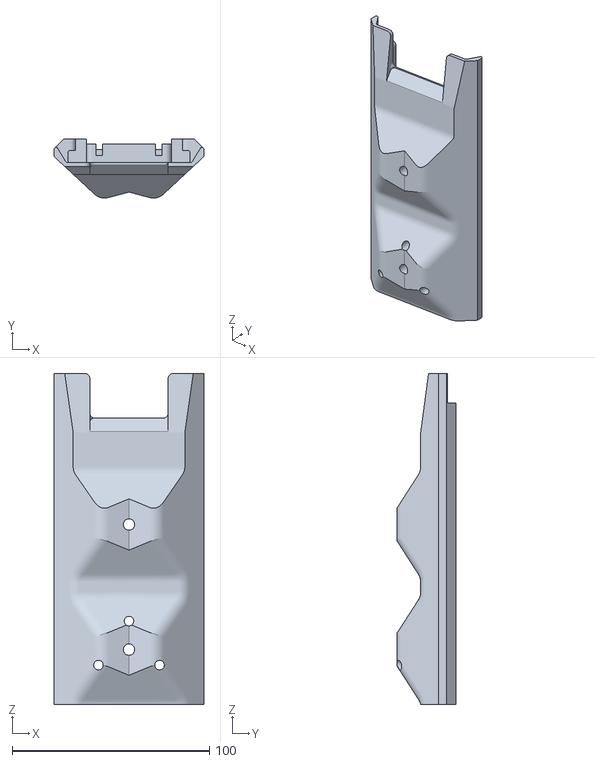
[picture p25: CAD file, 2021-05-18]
EBike Battery STL Files/Battery Mount Base_Thin.stl
76.0 x 30.1 x 168.0

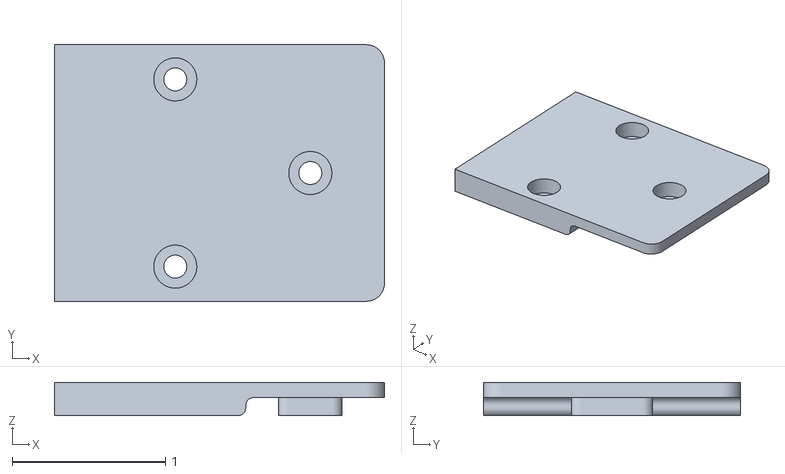
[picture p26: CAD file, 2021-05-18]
EBike Battery STL Files/EBike Battery Mount Lid.stl
2.15 x 1.67 x 0.217

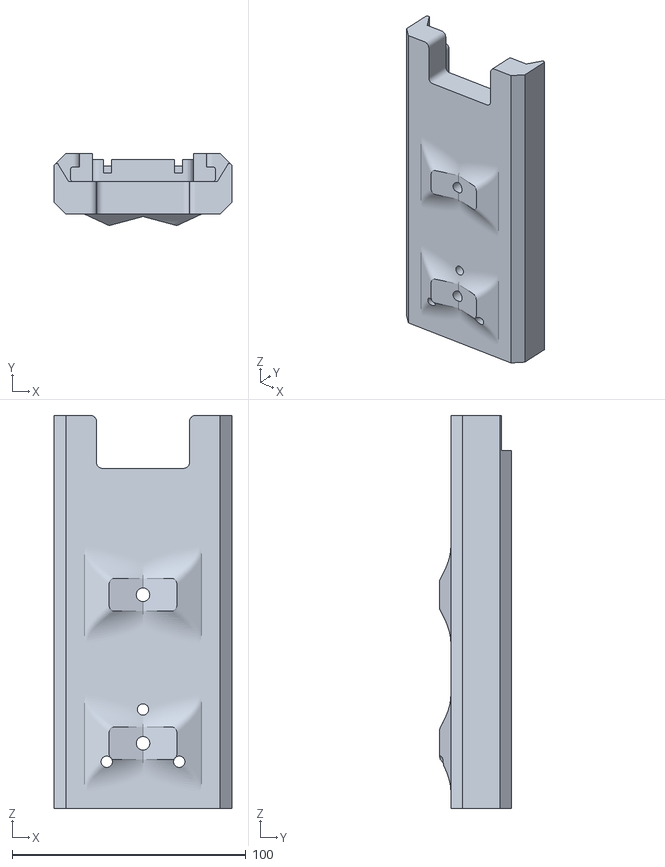
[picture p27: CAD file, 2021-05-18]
EBike Battery STL Files/Battery Mount Base_Thick.stl
76.0 x 30.9 x 168.0

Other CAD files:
EBike Battery Mount Fusion 360 Files/Battery Mount Base - Thick.f3z
EBike Battery Mount Fusion 360 Files/Battery Mount Base - Thin.f3z
EBike Battery Mount Fusion 360 Files/EBike Battery Mount Lid.f3d
EBike Battery Mount Fusion 360 Files/Female XT-60 3D Model.f3d
EBike Battery Mount Fusion 360 Files/Power Timer Contact 3D Model.f3d
EBike Battery Mount Fusion 360 Files/RYOBI 40V 3D Model.f3d

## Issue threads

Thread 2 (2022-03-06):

Missing information about control and sensor systems.

TheGuildTV, 2022-03-06:
It's a great project. It would be very helpful if the team could complete the documentation to help others build along.
The project B.O.M. and instructions are missing information about the source and specification of following components:

Motor controller
Cadence sensor (if used)
Brake sensors (if used)
Sysem info display (if used)
Throttle (if used)

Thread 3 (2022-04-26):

Ryobi 40V batteries are actually 36v. 40V 4ah is 144 Wh not 160 Wh

f0lie, 2022-04-26:
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

The Ryobi 40v is higher than the nominal voltage of the batteries which is 3.6V x 10 = 36V. In other e-bike batteries, you see 36V because they multiply the nominal voltage. Ryobi market doesn't do this and goes with 40V. This is technically still true because these batteries have a range of 4.2V to 2.5V https://www.powerstream.com/p/INR18650-25R-datasheet.pdf

The batteries themselves have a Wh rating and if you do 144/4 you get 36V which is the nominal voltage of the battery.

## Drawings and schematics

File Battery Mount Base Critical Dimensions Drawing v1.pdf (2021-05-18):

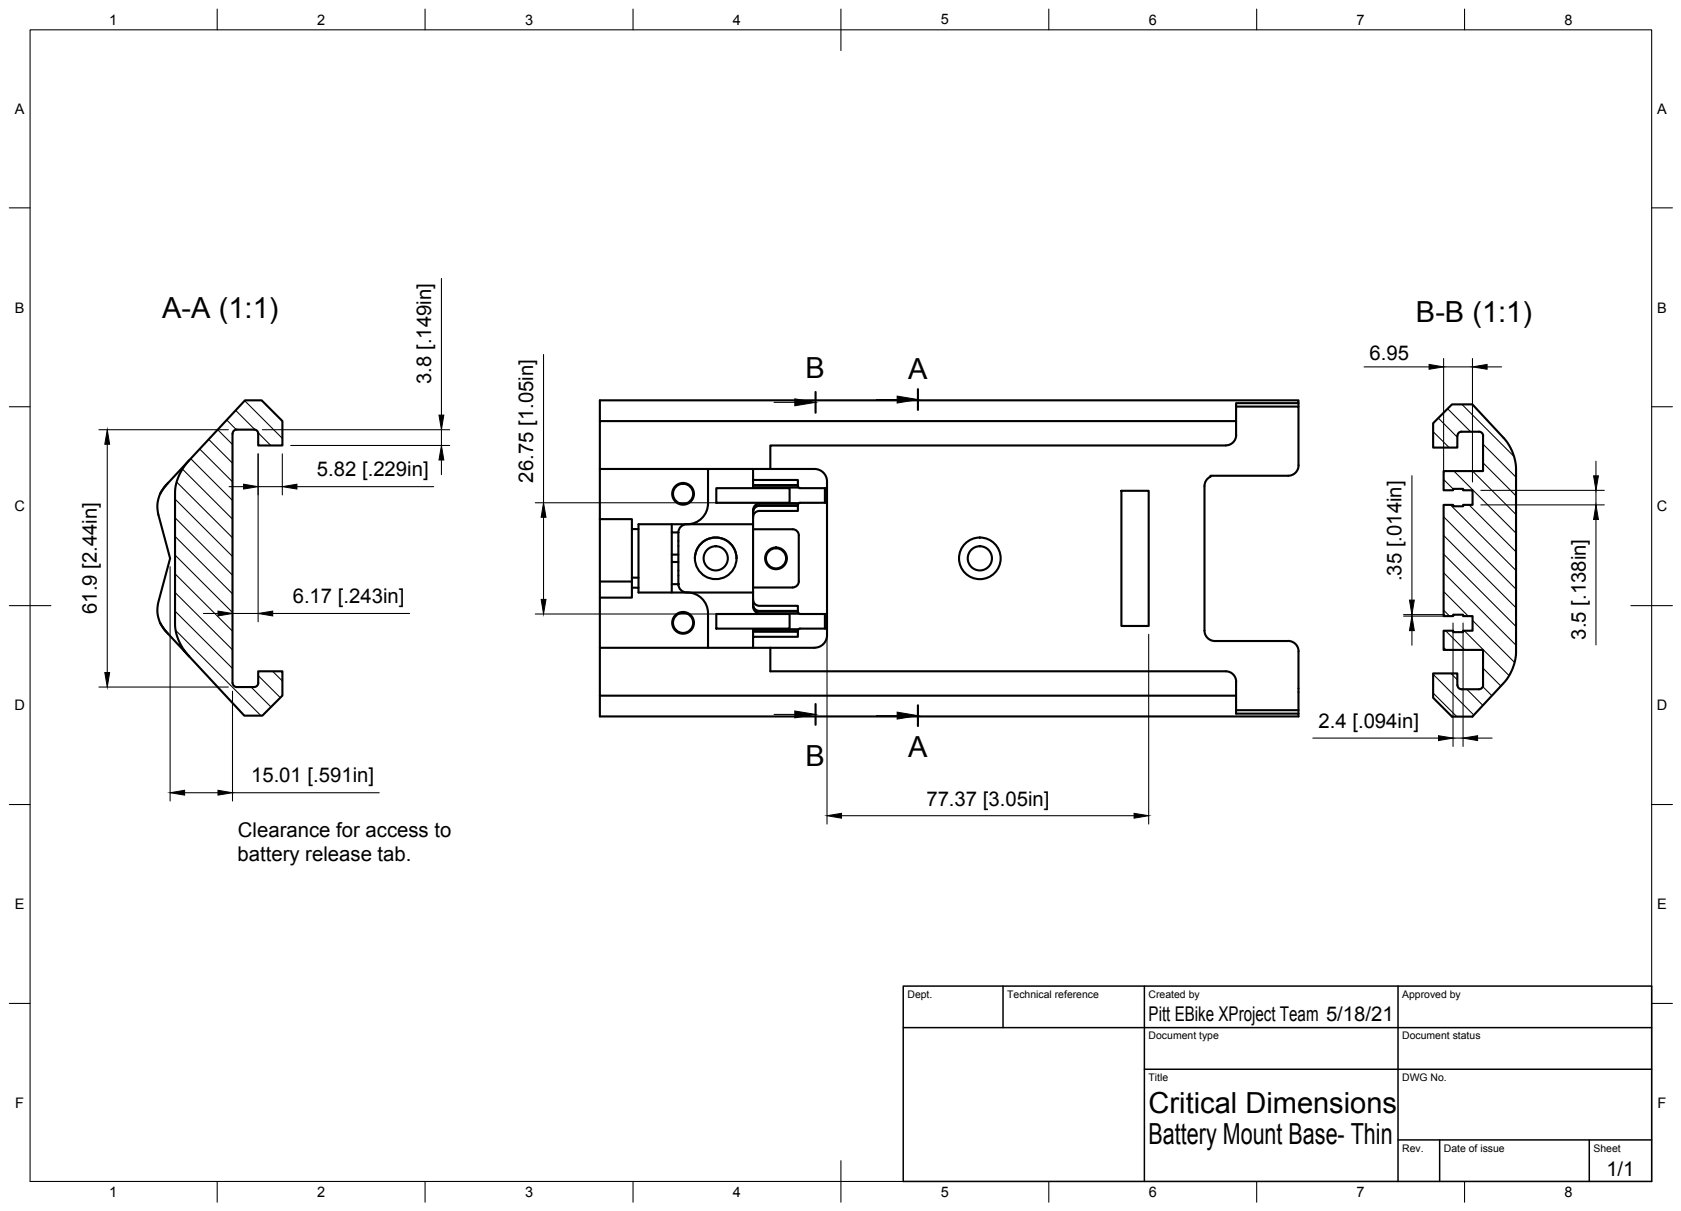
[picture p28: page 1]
Title; DWG No.; Rev.; Date of issue; Sheet

Clearance for access to
battery release tab.

Dept. | Technical reference | Created by Pitt EBike XProject Team 5/18/21 | Approved by

Document type | Document status

Critical Dimensions
Battery Mount Base- Thin

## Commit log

2021-05-07 Upload fusion files
    [Battery Mount Base - Thick.f3z, Battery Mount Base - Thin.f3z, EBike Battery Mount Lid.f3d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]
2021-05-18 uploaded stl files and critical dimension drawing
    [Battery Mount Base_Thick.stl, Battery Mount Base_Thin.stl, EBike Battery Mount Lid.stl]
